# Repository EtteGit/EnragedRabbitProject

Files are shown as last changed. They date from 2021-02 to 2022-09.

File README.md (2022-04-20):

# EnragedRabbitProject

Welcome to the Enraged Rabbit Project Github page!

This project aims to bring multimaterial capabilities to 3D printers using a single Direct Drive toolhead. While this project is mainly dedicated to be used on VORON printers, it can also be used (or adapted) on any 3D printer that runs Klipper, and potentially RRF.

You like this project? You want to support me and my work, help me bring new cool stuff to the community? Well you can tip me here :


## Table of Content
- [Changelog](#changelog)
- [Showroom](#showroom)
- [Videos](#videos)
- [Details](#details)
- [BOM](#bom)
- [Acknowledgements](#acknowledgements)
- [FAQ](https://github.com/EtteGit/EnragedRabbitProject/tree/main/Documentation/FAQ)
  - [Carrot Patch](https://github.com/EtteGit/EnragedRabbitProject/blob/main/Documentation/FAQ/FAQ_ERCP.md)
  - [Carrot Feeder](https://github.com/EtteGit/EnragedRabbitProject/blob/main/Documentation/FAQ/FAQ_ERCF.md)
 
## Changelog
- **April 4th 2022 :** Minor fixes and updates, check the new last page of the manual for tuning the last check of the load sequence
- **March 23th 2022 :** Revamp of ERCF unload sequence during a print, possibility to use stallguard capabilities to detect selector blockages, new encoder cart and much more
- **October 23th 2021 :** Update of the ERCF Macros and python module and added first part of manual Slicer setting section.
- **October 15th 2021 :** Added AfterBurner Clockwork toolhead sensor and associated manual sections.
- **October 7th 2021 :** Updated SwitchWire mount, LGX on AfterBurner toolhead sensor and associated manual sections.
- **October 1st 2021 :** Update including VORON SwitchWire mount, new Galileo Clockwork Toolhead sensor, additions to the manual and a few others things!
- **September 24th 2021 :** The ERCF V1.1 macros and python module are out! Also an updated manual (with the setup and calibration steps) and additionnal stuff for EASY BRD users! Have fun!
- **September 17th 2021 :** The ERCF V1.1 assembly manual, STL files and the STEP file are now released! You'll find the manual in the "Documentation" section now, and the manual will keep growing with setup, tuning and slicer guides. A non-exhaustive patch note can be found in the Carrot_Feeder folder. Finally, note that the new software part of the ERCF V1.1 is not out yet, and the ERCF V1.1 hardware cannot be used with the ERCF V1.0 macros. V1.1 software will be released in a few days. Happy printing and assembly!
- **September 14th 2021 :** Updated the BOM to ERCF V1.1 (release coming soon! tm) and added the new, incoming Toolhead Sensor BOM (bottom tabs)
- **June 4th 2021 :** TopHatLockers and related (servo arm, TopGearHat, macros) have been released to the main branch, from the EarlyDevAccess branch. If you're already running EarlyDevAccess stuff, that won't change anything for you
- **June 2nd 2021 :** Release of Carrot Patch V1.1
   - Increased handles section near the threaded insert for more robustness
   - Removed useless chamfer on feet bottom screw holes and increased hole depth (one can now properly use M3X8 SHCS to secure the Carrot Patch on 2020 extrusions)
   - Fixed several parts lengths//size that impacted the buffer wheel installation. Now the wheel should slightly touch both side walls (to avoid any possible gaps) while being able to turn (but not freely, which is on purpose)
   - Buffer Cross bottom arm is now secured using a M3X20 SHCS screw that comes from the bottom (that is also securing the left feet of the Carrot Patch)
   - Buffer Cross ECAS insert has been tuned, reinforced and a "bridge" shape has been added. Inserting the ECAS will no longer crack the plastic
   - Increased the size of the Buffer Cross "pillar" that sits between the two PTFE paths (some users previously reported fragilities due to the lack of matter for this pillar)
   - Updated the assembly manual, BOM and the CAD accordingly
   - Only parts that did not change are : [a]_Buffer_Wheel, [a]_Latch, [a]_Sliding_Arm, Buffer_Axis, Ptfe_Entry_ECAS and Ptfe_Entry_M10

## Showroom

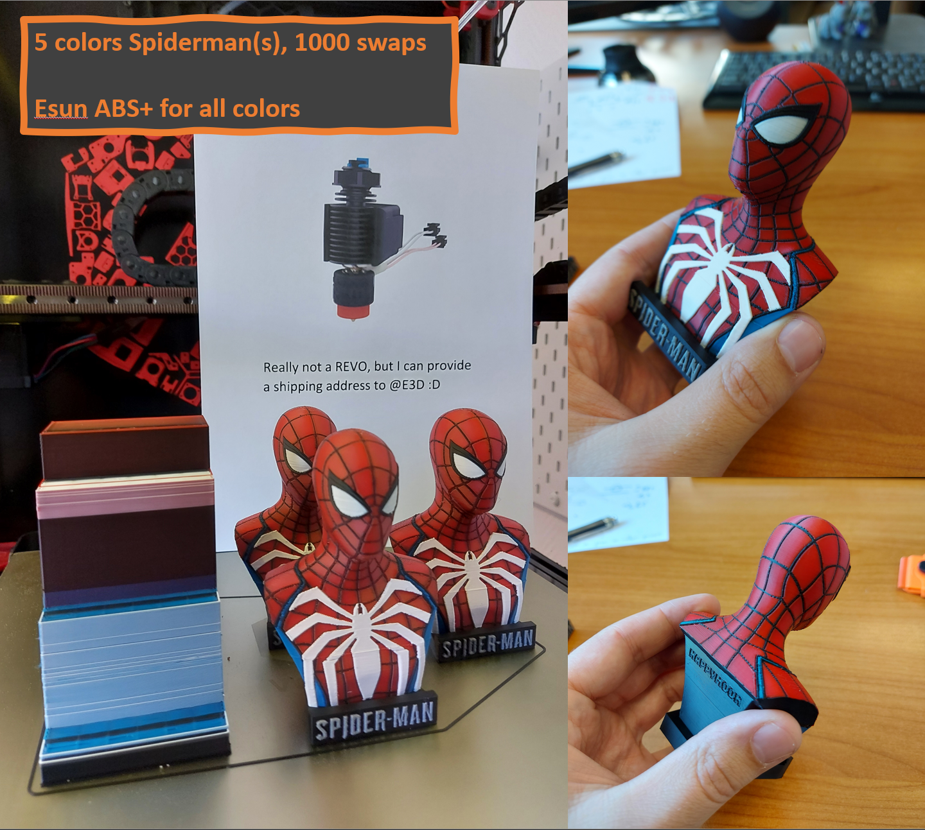
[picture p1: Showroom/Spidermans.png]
Spidermans
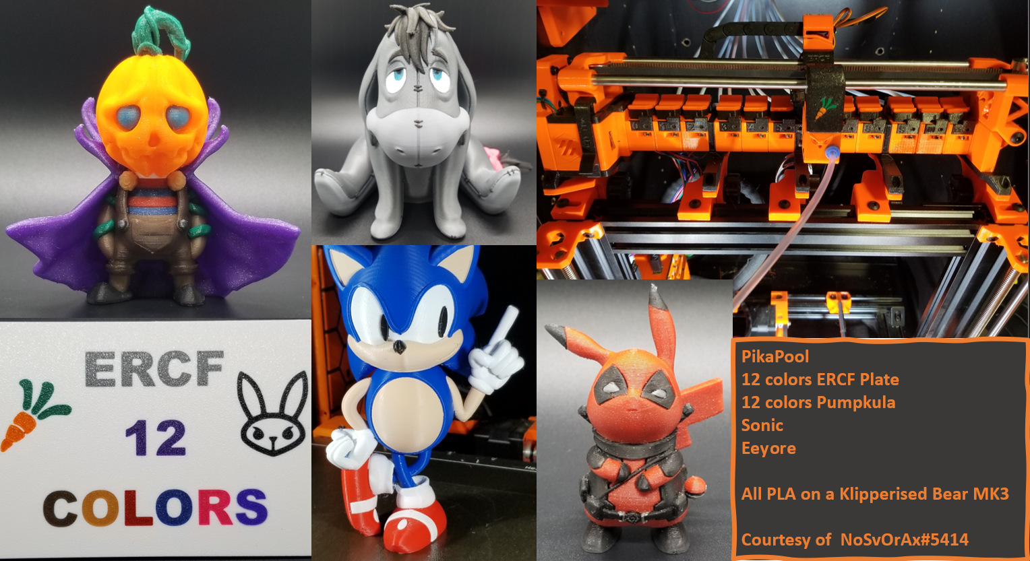
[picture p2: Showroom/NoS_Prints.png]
NoS_prints
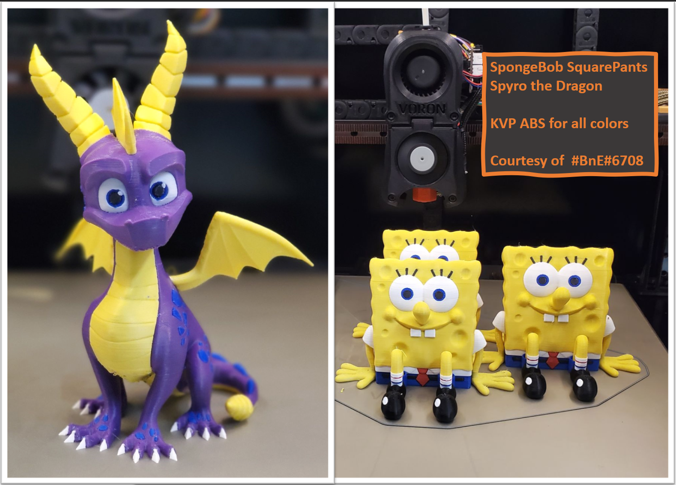
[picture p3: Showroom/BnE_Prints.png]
BnE_Prints
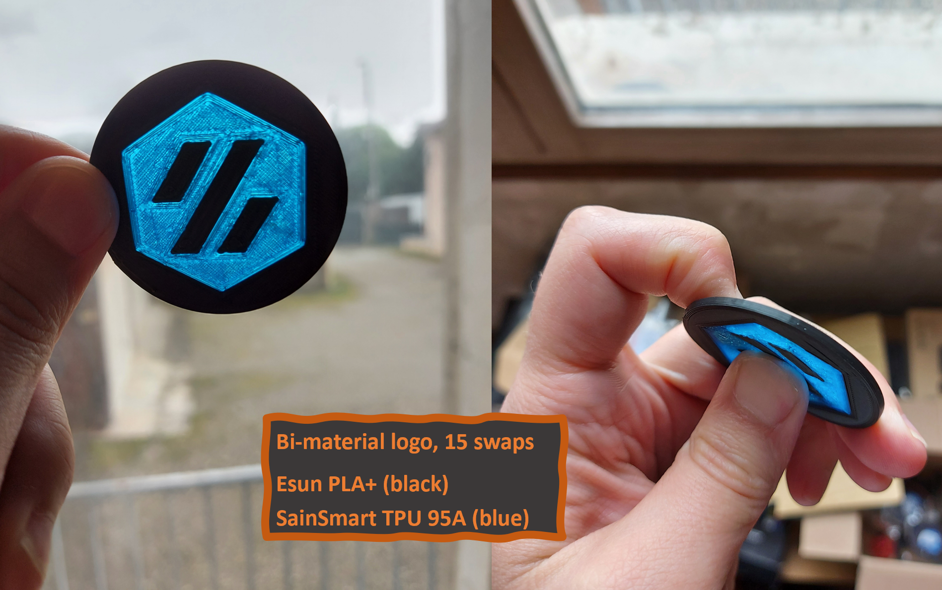
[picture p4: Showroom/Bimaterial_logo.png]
Voron Logo TPU
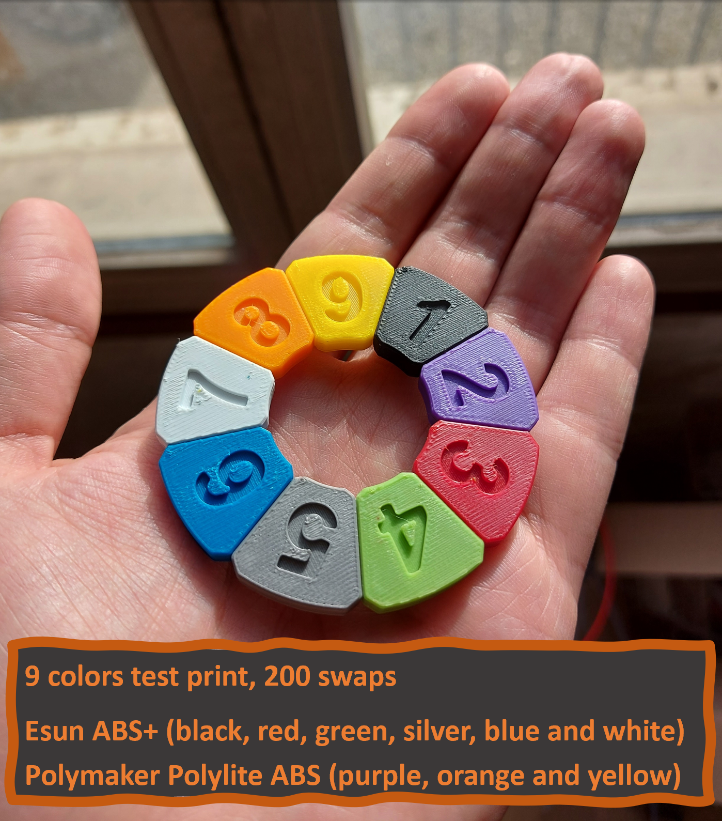
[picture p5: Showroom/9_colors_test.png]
9_colors_test


## Videos
Here are videos of the system in action. I need to release more videos...

https://streamable.com/3lo192

https://streamable.com/cjl2iz

## Details

There are 4 components so far : 
 - **The Enraged Rabbit Carrot Feeder (ERCF)**. The Carrot Feeder allows to use a high number of different filaments (tested up to 9 channels so far) and feed them, one at a time, into the printer toolhead. The ERCF gear motion system (i.e. what is used to push and pull the filament) is based on the Voron Design M4 extruder. The ERCF was inspired by the Prusa MMU2 and the Smuff.

  Carrot FeederCarrot Feeder 2
 
 - **The Enraged Rabbit Carrot Patch (ERCP)**. It is a light spool-holder and buffer combo to help you deal with the filament  
management issue associated with multimaterial systems.
 
 Carrot PatchCarrot Patch 2
 - **The Enraged Rabbit King's Seat (ERKS)**. The King’s Seat is a pellet-purge system to remove the need for a wipe-tower and make faster filament purges. This system is designed for Voron V2s only so far.
 - **The filament sensor** : a filament sensor system located below the extruder gears to check proper loading and unloading of filament.
  
Note that this is a work in progress !!
 
Only the King's Seat is yet to be released !
 
## BOM
 The BOM for those components can be found [here](https://docs.google.com/spreadsheets/d/1A_qeNeaVprh_iPbvLcLjvJ2o2NfCzjuJam3K3RkWW0w).
 
## Acknowledgements

Thanks to the VORON Design devs and VORON discord members for the discussions and support, with a special thanks to the #honhonhonbaguette-FR members and @Tircown#8715!!

Thanks to Fabreeko, DeepFriedHero (DFH), Blurolls and many others for supporting this project!

Ette

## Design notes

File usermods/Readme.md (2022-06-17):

# Mods 
This Folder contains modifications for the Enraged Rabbit

## Table structure

Update the following table with the information about your mod:
- Your name
- A link to your sub-folder
- A short description of your mod
- The component the mod is designed for. Use `:heavy_check_mark:` for :heavy_check_mark:,`:x:` for :x:

like so:
`
| Creator | [Mod title](link) | Description | :x: | :x: |`

| Creator | Mod title | Description | Feeder | Patch |
| --- | --- | --- | --- | --- |
| TheWarolf | [AB Toolhead Sensor](./AB_Toolhead_Sensor) | Makes the standard AB clockwork "smart" by inserting filament sensors in the toolhead. Uses microswitch + 7mm steel ball combo. | :heavy_check_mark: | :x: |
| Tircown | [Bearing_Block_Passthrough](./Bearing_Block_Passthrough) | Allows to do tests or add a temporary spool without taking apart the full setup while still benefit from the sensors of ERCF. | :heavy_check_mark: | :x: |
| EtteGit | [Closed_Exhaust_Plate](./Closed_Exhaust_Plate) | Replaces the nominal V2 exhaust parts with a close, sealed plate. | :x: | :x: |
| TheBelin | [EasyPatchLoader](./EasyPatchLoader) | Makes it easier to load Carrot Patch. | :x: | ✔️ |
| Drachenkaetzchen | [Extrusion Mounting Brackets](./Extrusion_Mounting_Brackets) | Extrusion mounting brackets to pre-assemble the ERCF and/or the ERCPs | :heavy_check_mark: | :heavy_check_mark: |
| Tobi0892 | [IKEA Drybox Carrot Patch](./IKEA_Drybox_Carrot_Patch) | Puts the Carrot Patch into a sealed 10.6l IKEA 365+ box to maintain ~10% humidity. | :x: | :heavy_check_mark: |
| fsironman | [JST-SM-Connectors](./JST-SM-Connectors) | Modifies the M4 Arm to use JST-SM instead of microfit connectors | :heavy_check_mark: | :x: |
| simon-adriaanse | [LGX_Mount_TL_IR_Sensor](./LGX_Mount_TL_IR_Sensor) | This mount is for the TriangleLabs IR sensor. | :heavy_check_mark: | :x: |
| th3fallen | [LGX_Toolhead_Sensor](./LGX_Toolhead_Sensor) |  | :heavy_check_mark: | :x: |
| Falovan | [Narrow KVP Spool Ramp](./Narrow_KVP_Spool_Ramp) | Adds a ramp to the carrot patch to prevent narrow spools from catching | :x: | :heavy_check_mark: |
| th3fallen | [Orbiter_Toolhead_Sensor](./Orbiter_Toolhead_Sensor) |  | :heavy_check_mark: | :x: |
| jorender | [Printable_drag_chain](./Printable_drag_chain)  | A printable cable chain suitable for use with the Enraged Rabbit Carrot Feeder | :heavy_check_mark: | :x: |
| claytono | [Skirt-Microfit-Inserts](./Skirt-Microfit-Inserts) | An iteration on dvorak74's Micro-Fit inserts, based around meteyou's fantastic G-code button mod. | :heavy_check_mark: | :x: |
| Drachenkaetzchen | [Upside Down ERCP](./Upside_Down_ERCP) | Mod to allow mounting the ERCP upside down, for example, below a shelf | :x: | :heavy_check_mark: |
| str1pes | [MagFeet](./MagFeet) | Easy mounting/removal for 2020 extrusions | :x: | :heavy_check_mark: |
| joey2point0 | [4L_Filament_Buffer](./4L_Filament_Buffer) | Utilizes 4L cereal box container to make a sealed filament buffer. | :x: | :heavy_check_mark: |
| ~MHz | [Orbiter_V1.5_V2_on_AB](./Orbiter_V1.5_V2_on_AB) | Yet Additional Orbiter v1.5 Mechanical and Inductive Extruder to Toolhead adapter and a WIP Orbiter v2 Inductive Extruder to Toolhead adapter  | :heavy_check_mark: | :x: |

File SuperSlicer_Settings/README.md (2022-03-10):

# SuperSlicer settings

I'm using SuperSlicer (https://github.com/supermerill/SuperSlicer) with my ERCF.

Here is a collaborative, open table to share [proper purging volumes](https://docs.google.com/spreadsheets/d/11onBwd85u0-9houRi6wMT2FBWrvbKk8fzwE3qLjkN1w/edit?usp=sharing). Please respect the table layout and don't delete//edit other people's inputs :) .

Here are my SuperSlicer settings related to the multimaterial :

## Printer Settings
#### Custom G-code
Tool change G-code : T[next_extruder]

#### Single extruder MM setup
Cooling tube position : 40mm
Cooling tube length : 20mm
Filament parking position : 85mm
Extra loading distance : -83mm
High extruder cyrrebt on filament swap : off

Important : those settings are tested for a Dragon Normal Flow hotend! If you have a different hotend, you'll have to tune those numbers.

## Filament Settings

Each filament (brand, type or even just color) behaves differently. The goal of tuning those filament settings is to end up, at every single filament change, with a nice filament tip.

What is a nice filament tip?? It's a tip withtout long hairs, without blobs, with a proper, well defined, diameter. It should more or less look like a nice spear end.

Filament tip tuning is THE MOST IMPORTANT setting in your MMU setup, period. So take the time to tune those, it's really worth it!
The default filament settings associated with the PrusaMMU2S profile in prusa//super slicer are a very good starting point!

Esun ABS+ : use default multimaterial settings from the MMU2S profile (PrusaABS filament profile), and add a skinnyDip string reduction sequence with 42mm insertion distance, 0ms of pause, 33mm/s speed to move into the melt zone and 70mm/s speed to extract from the melt zone

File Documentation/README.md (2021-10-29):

# Enraged Rabbit Project Documentation

All the manuals for assembly, setup and tuning related to the Enraged Rabbit Project are here.
You can also find the FAQ in its dedicated folder.

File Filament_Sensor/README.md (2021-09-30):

Readme for Filament Sensor

# General guidelines and informations
The toolhead sensors are based on a hall sensor, design is from @Tircown.

Galileo ClockWork is available.

AfterBurner ClockWork and LGX on AfterBurner will be released soon.

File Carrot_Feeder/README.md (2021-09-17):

# ERCF V1.1 Patch Note (non exhaustive)
This is a major update. If you already have a, ERCF V1.0, please reprint all the parts for V1.1. Feet anchoring points are unchanged.

## Hardware:
### Filament Blocks:
- Updated filament path to limit unselected filament being pulled or pushed by the rotating gear. The grip on the filament is also drastically improved
- Fixed the ECAS insert slot
- Removed the threaded insert version as the direct plastic tapping was sufficient
- New and improved number tag plate (easy to install and remove, much more robust than before)
- Added magnetic gates at the exit of each filament block : using a M3 Steel washer and magnets, the filament path of each filament block will be closed at the filament block exit when the selector is not in front of it, ensuring that no unselected filament can stick out and block the selector cart during a tool change
### Top Hats :
- Redesign of the Top Hat arm to avoid it's ejection when opening the filament block latch
- Top Hat Lockers are now easier to print (more contact area with the print surface)
- New slide-in mechanism for the Top Hat Lockers
- Top Hat Locker will no longer touch the Filament Block Latch, which is no only touching the Top Hat
- BMG gear can no longer be installed in the wrong orientation in the Top Hat
- Moved the servo pressure point on the Top Arm Locker to have a better grip on filament
### Gear Box :
- Gear motor is now a low rotor inertia NEMA 14, allowing a smaller footprint, quieter operation and faster loads and unloads (NEMA 17 motors are still 100% compatible)
- Added a bearing on the Gear Box Back to better constrain the 5mm D-Cut shaft and remove potential longitudinal play
- Motor Arm infamous overhang is now easy to print
- Added a customisable, multicolor logo on the front, which is easy to change
- Minor fixes (micro switch lever colliding with 3D printed part, more plastic matter behind the left side latch threaded inserts...)
### Bearing Blocks :
- Added foot to improve global stiffness, especially for long units. It can be install and removed easily without dismounting the unit
### Selector Motor Support :
- Fixed the 8mm rod hole issue (same for the Idler Block)
- Fixed the selector motor screws issue
### Selector Cart :
- Old filament sensor is gone. Now there is an amazing encoder, idea and design by @Tircown! Encoder fits in the ERCF selector cart, has a 1.3mm resolution and can keep up with very fast movement (20cm/s +). Allows to precisely track filament load and unload, potential clogs during a print and is also used as filament runout sensor
- New servo ref. Easier to source, quieter and much cheaper than V1.0 model, works well with the new Top Hat Locker and - Filament Blocks design. V1.0 servo model is still 100% compatible
- Mystery stuff hidden behind the new selector cart door, can you guess what it is from the charade hidden in the ERCF?

## Software:
To use the new selector encoder, part of the software have to be done in the python part of Klipper. The ERCF V1.1 software will now include a .py file and the usual cfg files. The GCODE macros are still in use, but are much smaller.

Regular update and improvements will be done on the software side, as using the python part of Klipper allows for much more complex and fancy stuff to be done.

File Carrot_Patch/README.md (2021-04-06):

This directory contains the files necessary to print and construct the Carrot Patch spool holders.

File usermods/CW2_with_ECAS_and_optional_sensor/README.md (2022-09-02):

## Clockwork 2 with ECAS fitting, with or without ball bearing filament sensor

This version of the Clockwork 2 extruder adds an ECAS fitting to the filament
input port. The ECAS serves the same purpose as a screw-in PC4 fitting: to retain
the PTFE tube during ERCF operations so it doesn't pop out. 

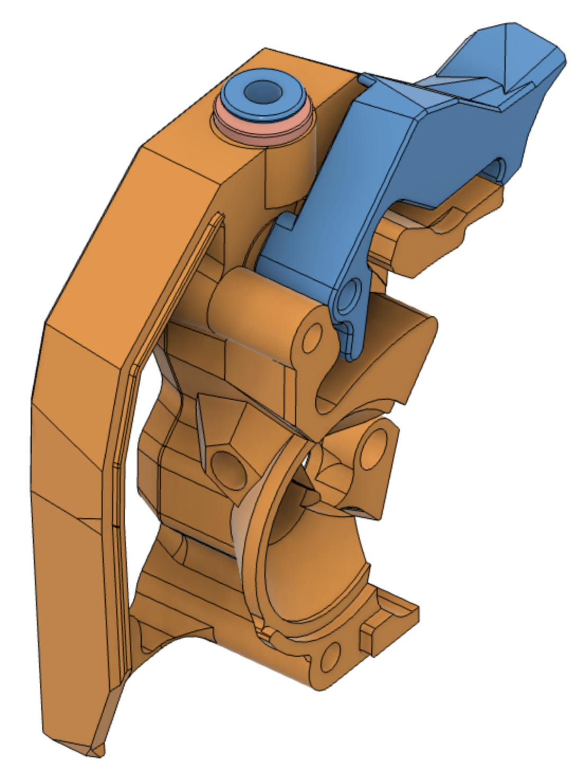
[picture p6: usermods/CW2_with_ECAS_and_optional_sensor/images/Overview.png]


Optionally, you can print a version that includes provisions for a mechanical filament
sensor that uses a ball bearing and microswitch. See below.

The basis for these designs is the VoronDesign/Voron-Stealthburner project on GitHub as
of August 18, 2022, git commit b2cf2c2. Here are a
[link to that commit](https://github.com/VoronDesign/Voron-Stealthburner/tree/b2cf2c2c0436d734181688ae3019b9dffb835b8b) 
and a [link to the current version](https://github.com/VoronDesign/Voron-Stealthburner) 
of the Voron-Stealthburner project.

The version of Voron-Stealthburner on which this mod is based postdates RC1. 
Both the CW2 main body and the 
latch have been updated relative to the RC1 release of Voron-Stealthburner.
However, RC1 versions of other parts **are** compatible with this main body and latch.

The parts in this mod **are not** compatible with pre-RC1 versions of the Clockwork 2.
Please see the pinned mod in the Discord #ercf_questions channel if that's the CW2
you want to modify.

## ECAS-only (no filament sensor)

For the ECAS-only version, you just need to print the main body
and the latch. The rest of the parts are identical to the standard CW2.

Press-fit the ECAS into its dedicated hole as described in the ERCF documentation. Done!

## ECAS and filament sensor

The filament sensor included here uses a 7mm ball bearing and a standard microswitch. It
is *not* a direct port of the standard ERCF toolhead switch, which uses a Hall-effect sensor.
The mechanical version seems to be somewhat less susceptible to jamming and misreading.
However, it does introduce a small amount of friction on the filament path. 

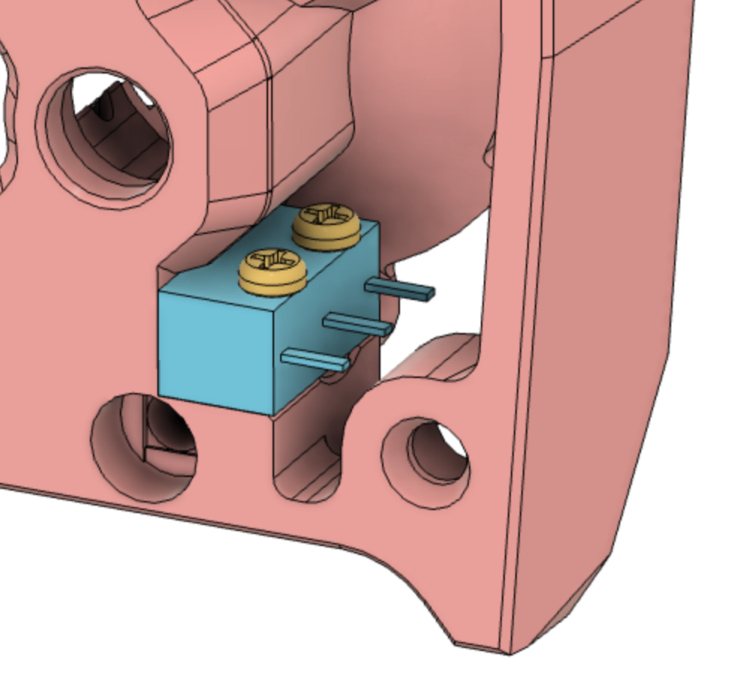
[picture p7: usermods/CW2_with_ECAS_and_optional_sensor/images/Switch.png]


### Bill of materials

You will need:

- An Omron D2F-series microswitch with lever, or equivalent (e.g., D2F-01L, see below)
- Two M2x10 self-tapping screws
- One 7mm ball bearing (stainless steel is fine, does not need to be magnetic)
- One ECAS fitting

According to Omron's CAD files, the plunger on
a D2F without a lever is shaped slightly differently from the plunger on a lever
switch. This mod is designed for a lever switch even though the lever isn't used. 
Plunger-only
switches might work fine. I just don't know for sure.

The mod also assumes that the switch's operating force is the standard 1.47 Newtons.

See Omron's [D2F data sheet](https://components.omron.com/us-en/datasheet_pdf/B036-E1.pdf)
for details on decoding all the variants of this switch. The model number should end with an
L and should not contain an F. Any voltage or current rating is fine. You probably want
standard PCB terminals, but any variant should work. However, be sure not to block the
cutout next to the switch, as that's a through-way used when bolting the CW2 to the
carriage.

### Operating principle

Here's a cutaway view of the sensor when assembled:

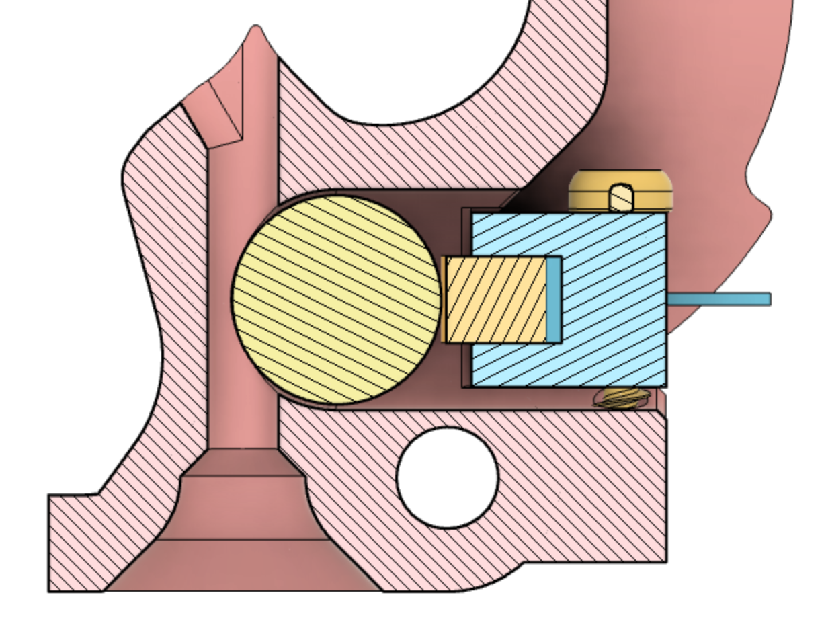
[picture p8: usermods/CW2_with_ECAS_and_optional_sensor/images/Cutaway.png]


The ball bearing intrudes into the filament channel. When filament is present, it
pushes the bearing aside, causing it to activate the switch. 

### Assembly instructions

- Remove the lever from the switch. 

- Print the test block.

- Insert the ball bearing into the test block. It should pop in with just slight pressure.

- Screw the microswitch into the test block. Make sure the plunger of the microswitch is 
centered on the bearing. For Omron switches, the side with printing on it should be down.

- Make sure that filament can easily be inserted (even with a blunt end) and that 
the sensor assembly does not
add excessive friction.

- Use a multimeter to verify that the switch consistently activates when filament is 
present and deactivates when filament is removed.

- If you have problems with friction or failure to register filament, see the section
below regarding alternate STLs.

- Print the main body and the latch.

- Press-fit the ECAS into the top of the main body.

- Solder two wires to the switch and cover them with heat-shrink tubing.
Use the two outer leads for normally-closed mode, which is recommended.
Ignore or cut off the middle lead.

- Install the ball bearing and switch in the main body of the CW2.

- Install the new main body and latch on your CW2.

- This mod shortens the bottom end of the filament path by 3mm. So 
shorten the stub of PTFE tubing coming out the top of your hotend cartridge by 3mm.

- Once the new parts are installed on the CW2, you can bend the PCB leads coming 
out of the switch to direct the wires more naturally. Not much bend is needed if
you are using a standard cover and PCB.
Do not bend the switch leads downwards so
that they interfere with the wrench path for attaching the CW2 to the carriage.

- Add the appropriate connector to the other end of the wires, hook up, and configure
in the ERCF control files for Klipper.

### Alternates

If the test block seems to indicate that filament won't be reliably detected, or 
will be unreasonably pinched by the ball bearing, you can try the "tight" or "loose" 
variants from the Alternates folder.

- The tight version moves the ball bearing channel and the switch further
*into* the filament path. This *increases* friction, makes it *harder* to get 
filament past the ball bearing, and makes it *easier* for filament
to activate the switch.

- The loose version moves the ball bearing channel and the switch further
*out of* the filament path. This *reduces* friction, makes it *easier* to insert filament, 
and makes it *harder* for filament to reliably activate the switch.

I don't yet have data on other people's experience with this filament sensor design.
My hope is that the standard configuration will cover nearly all cases, but 
filaments and tuning
vary. The loose and tight versions are just there to give you a backup plan. Stick 
with the standard version unless you're encountering specific issues.

## Bug reports and suggestions

For problems or suggestions, you can file a GitHub issue against 
[my fork of the ERCF project](https://github.com/GarthSnyder/EnragedRabbitProject).

I am @Iatrodectus on Discord and @GarthSnyder on GitHub.

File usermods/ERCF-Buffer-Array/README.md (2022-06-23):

# ERCF-Buffer-Array

The Carrot Patch for the Enraged Rabbit Carrot Feeder has an integrated spool holder included. For people who store their spools in a drybox, this can be an issue. Either you have to store the buffer ring also in the dry box, which takes away space for filament spools, or one has to design a dedicated solution for the buffer ring outside of the dry box.

The Buffer Array solves this issue by dropping the spool holder and allows stacking up buffer rings side by side, called Buffer Array. One buffer ring element takes up 40mm of space (normal version) or 33.5mm (slim version). The Buffer Array is based on a modified main body so that all other required parts of the carrot patch can be re-used. The Buffer Array is modular an thus can be adapted to the size of your ERCF. For up to N=6, I also provide an integrated solution vor the V2.4, see image below.

Building a Buffer Array of length N>1 requires:
- the standard Carrot Patch parts:
  - 1x 608_Adapter.stl
  - 1x Buffer_Axis.stl
  - 1x Buffer_Cross.stl
  - 1x Buffer_Wheel.stl
  - 1x feet_x2.stl or Feet_cut_off.stl
- 1x "Buffer Array Start"
- (N-2)x Buffer Array Middle
- 1x Buffer Array End
- recommended for stability: multi-locker with or without guide for ptfe tubing
- 1x M5x30mm and 1x m5 lock nut
- 1x M3x20mm, 1x M3x8mm, 2x M3 heat insert (Voron version M3x5x4)
- 608ZZ bearing

If you already have old carrot patches, then you can recycle all parts except the heat inserts!
If you want only N=1 then there is also "Buffer array Stand-Alone" available.

If you want to integrate an 6x ERCF with buffer array and spool holder on your back of your V2.4 (350mm), then use the special multi-locker and spool holder in the " V2.4-Integration", see image below.

RL Triple Buffer Array

RL Triple Buffer Array

Overview Main_Body Types

Overview Main_Body Types

Overview Main_Body Types

V2.4-Integration

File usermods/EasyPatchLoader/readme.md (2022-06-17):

# ERCP Easy Load Buffer Wheel

This buffer wheel replaces the existing buffer wheel.

## To Load:
1) Feed the filament through the load tube.
2) Push the filament end into the slot on the side of the wheel, the curved profile should keep your filament secure.
3) Turn the wheel to load the buffer your required amount.
4) Position the wheel near the buffer exit fitting.
5) Unclip the end of the filament from the wheel and push it into the ERCF feed tube.

[Download STL](./STL/[a]_Buffer_Wheel_EZ_Loader.stl)

## Images
Easy Load Buffer Wheel
Easy Load Buffer Wheel Step 1
Easy Load Buffer Wheel Step 2
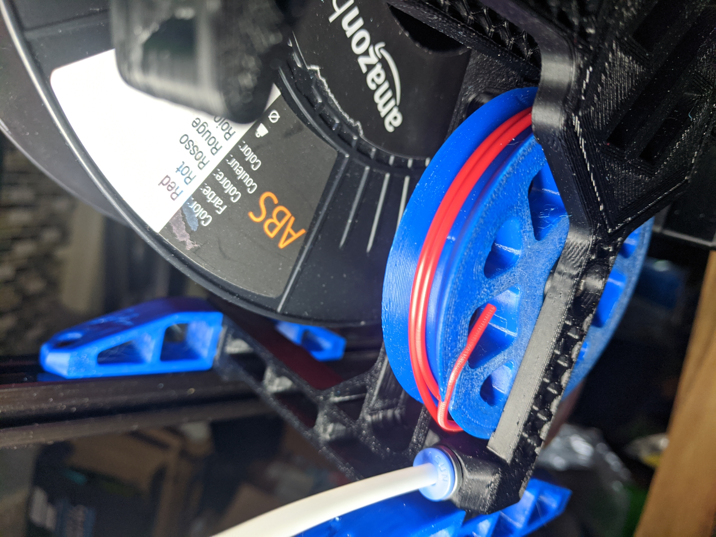
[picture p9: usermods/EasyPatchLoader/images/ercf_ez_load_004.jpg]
Easy Load Buffer Wheel Step 3

Easy Load Buffer Wheel Step 4
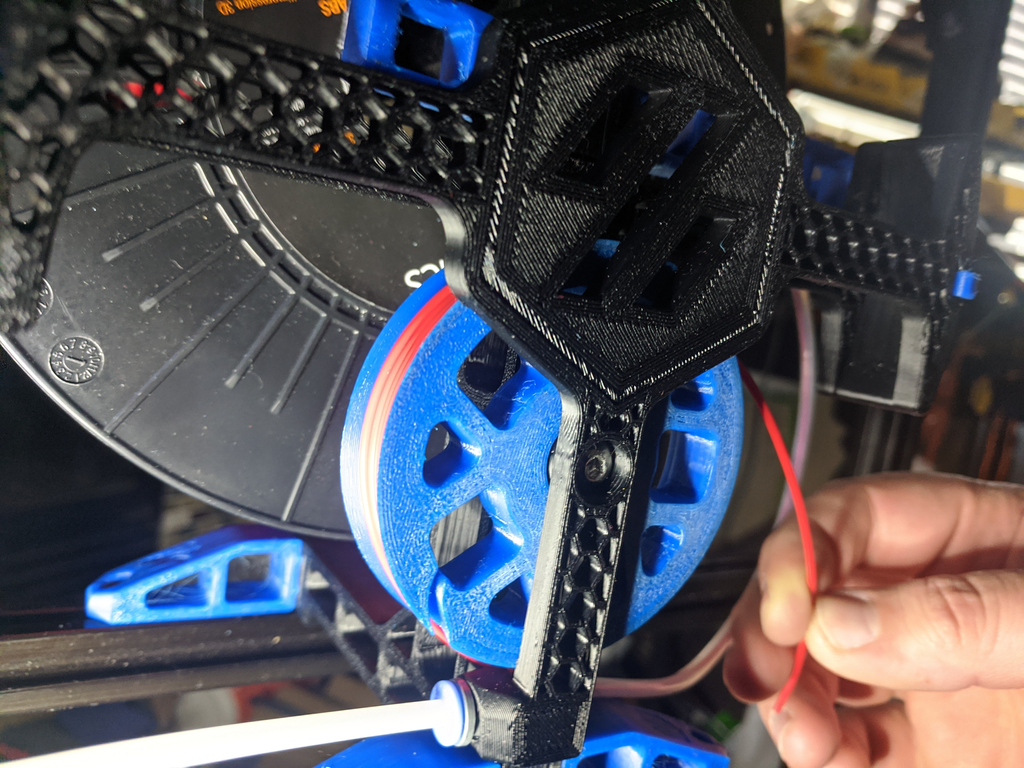
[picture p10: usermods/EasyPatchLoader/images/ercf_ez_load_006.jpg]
Easy Load Buffer Wheel Step 5


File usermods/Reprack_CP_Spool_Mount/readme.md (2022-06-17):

Carrot Patch spool mounting bracket for the [RepRack filament holder](https://www.prusaprinters.org/prints/129024-reprack-open-source-spool-holder-and-storage-syste). This is a cheap way to mount a bunch of filament to the wall above your printer.

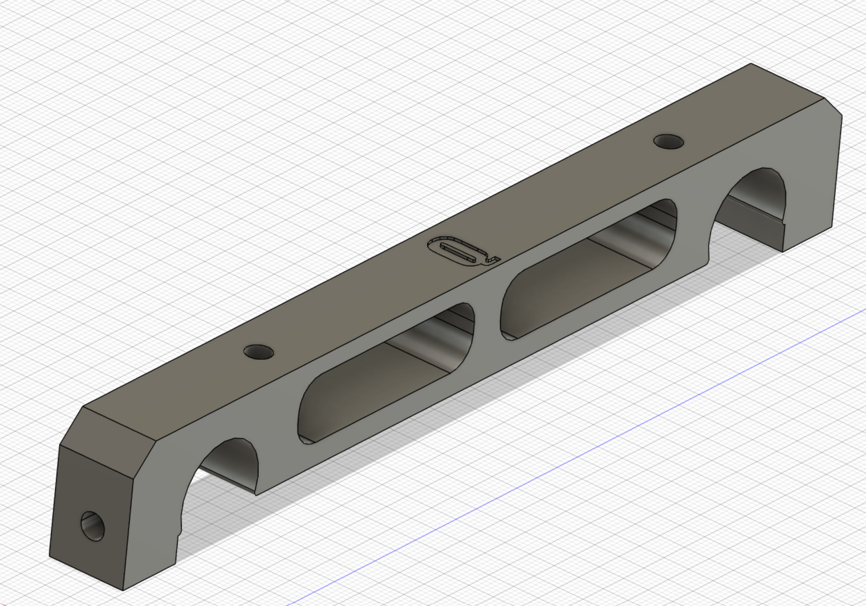
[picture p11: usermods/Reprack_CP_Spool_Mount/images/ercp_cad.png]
Fusion 360 Screenshot of the mount


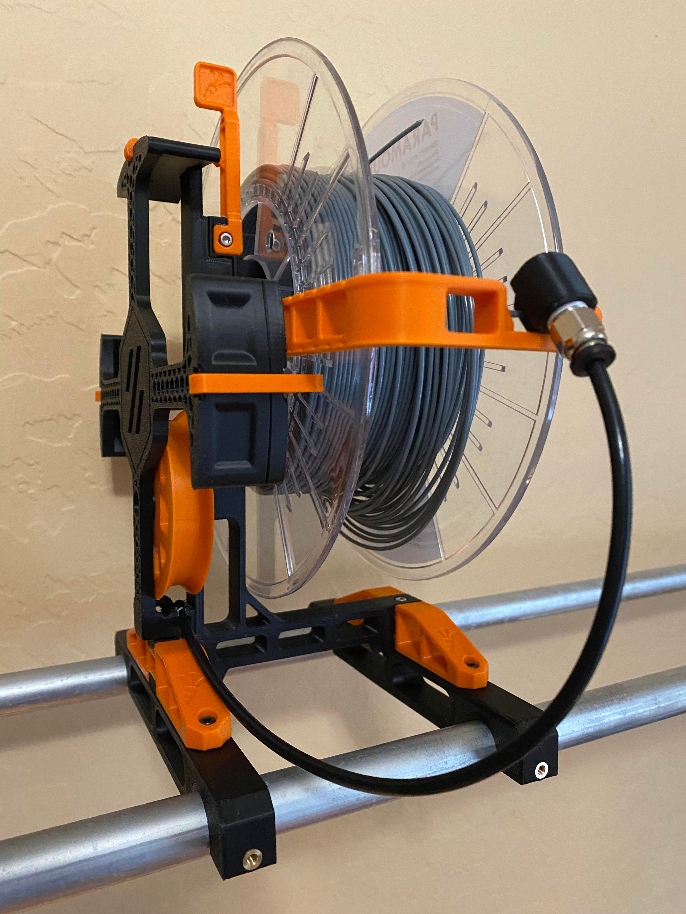
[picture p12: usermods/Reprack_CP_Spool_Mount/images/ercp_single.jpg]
Picture of a single fully assembled ERCP mount


# Assembly Instructions

1. Print as many mounts as you need
2. Install M3 heat inserts into the top two holes, and the side hole. Pro-tip: attach the heat insert using a short M3 bolt as a guide.
3. Attach the Carrot Patch spool with two M3x8 screws
4. Place the spool holder on the RepRack, optionally secure it with the front mount

# Version
* Version for non-covered tube: [Regular Version](RepRackErcfMount.stl)
* Version for Slip Rod Covered tube: [Slip Rod Compatible Version](RepRackErctMount_SlipRod.stl)

# Credit
* Regular Version: Designed in Fusion 360 by Danny Quist Discord: chamcham#6574
* [Slip Rod](https://www.printables.com/fr/model/135700-slip-rod-cover-for-reprack-and-repbox) compatible version: modified in ThinkerCAD by Flisher on Discord

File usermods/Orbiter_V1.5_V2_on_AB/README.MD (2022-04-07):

Here are some cobbled up ERCF tool head sensors:

- inductive filament sensor/adapter for mounting the Orbiter v1.5 (and v2?) on the AB.
- mechanical filament sensor/adapter for mounting the Orbiter v1.5 on the AB.

The Orbiter V2 inductive sensor adapter is a remake of the same thing on the Orbiter 1.5 I originally did for myself.

I've tested and was using the inductive Orbiter 1.5 on V2.2526.  However, due to suspected thermal sensitivity (while it worked 100% outside of the printer), once installed and heated, reliability dropped substantively.  As such, I have since migrated to a bearing/microswitch setup and have had zero reliability issues since then.  Mechanical is the way to go here, I perceive.

The inductive Orbiter 2 is an alpha/beta/POC until it is tested and proven to work.  One user mentioned slight variances of the two main mount holes, but never got back with required geometry changes.

Print in the orientation depicted in the project files - no supports needed.  I used ABS with a typical Voron profile (240/120 temps, 0.4 noz, 0.2 LH, 4 walls, 5 top/bot layers, 40% infill, ...).

## For the inductive flavor:

Inductive BOM needs:  1ea/2ea 6x3 magnets, one of the iron washers used in the gates, the hall effect sensor in the ERCF kit, 6ea M3 heat inserts, a M3x8, the printed extruder adapter parts (2 pcs total), and 2 short bits of bowden tube:

- one 8.25mm piece from the Extruder into the throat of the adapter 
    - https://i.imgur.com/SoOvUEF.jpeg
- one 20.25mm(?) piece between the adapter into the throat of the hot end
    - https://i.imgur.com/e6WDewI.jpeg

NOTE:  Before I switched to the mechanical switch, I planned to double check these measurements when next I had the extruder removed from the tool head, but that never happened.  These tube measurements are relevant in the context of an Orbiter v1.5 on the attached adapter and a traditional AB install of a Dragon HF HE.  If you are using a different HE, then start out with a longer lower tube length and trim down in an iterative manner to arrive at a snug fit.  If one is using the Orbiter v2, then follow a similar process to arrive at the correct length of the upper tube.  In any case, if you are able to advise, I'll add those lengths herein for different HEs or for the Orbiter v2, to help peeps wishing to make use of same.

ERCF assy manual page 80/81 are applicable as it relates to the innards.

I added a JST 2.0 3-pin connector after I hobbed out some material to make room for it (post processing ya know...), but one could just run wires to an inline disconnect at the tool head or similar.

https://cdn.discordapp.com/attachments/928716501480009768/938473912537350194/2022-02-02-11-36-55.png

ERCF Manual shows only 1 magnet.  I ended up needing to stack 2 (the top one is a bit proud but space isn't an issue on the 1.5 mounted to an AB carriage with this adapter).  https://i.imgur.com/W8hy9hX.png

There's some dialog about the sensor being pole sensitive, so maybe that is why I had to use two.?.  w/e - it works...  

https://cdn.discordapp.com/attachments/928716501480009768/938505236845330472/20220202_134303.mp4

EDIT:  Besides the sensitivity of the hall effect sensor wrt N/S poles of the magnets,  there are different magnet types and numerous types of hall effect sensors.  The hall effect sensor model that is in the kit has been vetted by Ette for stability and use as the tool head filament detector in the hot environment of an enclosed Voron print volume (it's rated to 150 C).  Also, note that these hall effect sensors are open drain devices - presenting a hi-z open when there is no filament detected and connected to ground when filament is detected.  This means that the signal input to the MCU should have the internal pull-up enabled (^) and have inverted logic enabled on said input (!):  https://i.imgur.com/XfR8kqq.png 

## For the mechanical flavor:

A .stl is provided.  If one desires to see how I did this in PS from a blank adapter, I have also provided a .3mf project file.  The .3mf needs to be opened and sliced in Prusa Slicer >=v2.4.1, as it makes use of Negative Space Modifiers to redact material from a blank adapter model for the bearing cavity, the microswitch/attaching screws, the JST 2.0mm 3-pin male header, and the wire path from the switch to the JST (I used 30awg silicone insulated (wirewrap) wires for same.  I slice the model and saved the gcode.  I then used Voxelizer to take the gcode and create a .stl from the sliced gcode.  The back way around, admittedly, but it works and helps me to avoid learning 3D CAD that much longer... ;)

BOM:

- 1ea printed adapter set (both front and back models)
- an Omron D2F-01 or similar (typical endstop switches)
- 2ea self-tapping M2.5 x 10mm screws
- 1ea 4mm (or 4.5mm*) Bearing
- 1ea JST 2.0 3-pin connector pair (male on the adapter, female on wire side)
- ~6" of 30AWG silicone insulated (or similar) wire

*The bearing cavity/throat was originally designed for a 4.5mm bearing, as I thought I had them on hand but nope, so I made use of a 4mm bearing and have experienced no issues.  It just works.  It's so much better than fighting with lines of flux... ;)

## Happy Printing!

Enjoy.

~MHz

(P.S.  Don't judge.  lol.  These were cobbled together from several models using Prusa Slicer as a CAD alternative.  I have absolutely zero/naught/nil 3D CAD skills, so this is the best I am capable of ATM. 🙂 )

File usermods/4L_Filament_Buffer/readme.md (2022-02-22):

# Filament Buffer Drybox - BETA

This buffer solution is still heavliy in beta, changes to the design will come out as issues and areas of improvement are identified.

[Link to repo](https://github.com/joey2point0/Filament_Buffer_Drybox)

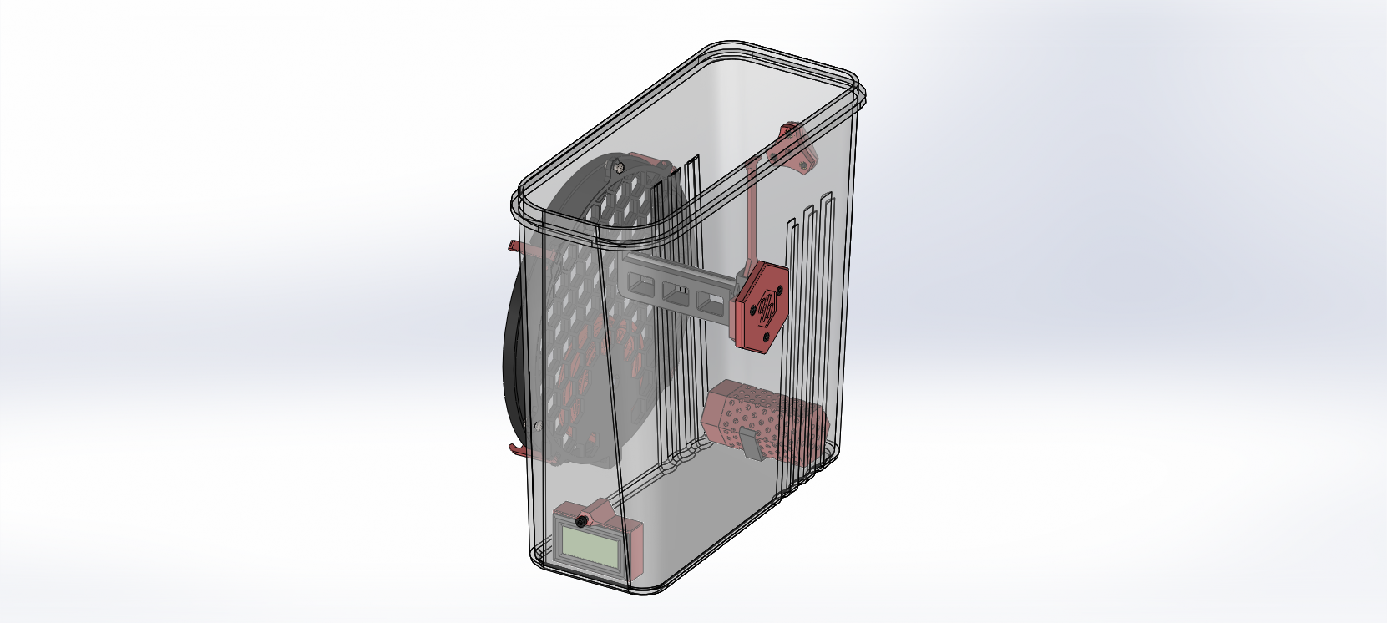
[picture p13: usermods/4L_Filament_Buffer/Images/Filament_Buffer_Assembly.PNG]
Filament Buffer Assembly


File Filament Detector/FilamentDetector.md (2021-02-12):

Readme for Filament Detector

# General guidelines and informations
Right now only the Galileo clockwork version prior to the latest release of beginning of February 2021 is available.
Version for the newest Galileo clockwork will be done soon, and so is the version for the regular Afterburner.

Check the assembly manual in this folder.

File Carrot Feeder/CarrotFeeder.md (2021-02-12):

Readme for the Carrot Feeder

# Printing guidelines
Use typical Voron parts printing guidelines (as found on the Voron Discord). No supports are needed.

For the Filament_Block part, you have the choice to use either the insert version or the no insert version. The M3 threaded insert on this part is tricky to insert, so you can simply screw the M3x16 in the plastic if you prefer. There are no real efforts on this screw, so choose the version you prefer (I prefer the threaded insert).

The support feet are either in 4mm or 5.5mm, depending on the Top//Back plate of your Voron.

The 'dome overhang' on the M4_Gear_Arm is an extreme torture test for the overhangs. It will probably not look good (but if your printer is properly tuned it will be ok). It's ok though, just clean it slightly if need be, you just don't want "stuff" hanging around.

You can use any number of Bearing_Block in your system, and wherever you want in-between your Filament_Blocks. Though the bar lengths from the BOM are calculated assuming you are using one Bearing_Block (of 5mm width) per 3 Filament_Block, starting from 3 blocks (i.e. 0 Bearing_Block for 1 to 3 channels system, 1 Bearing_Block for 4 to 6 channels systems etc.).

# Assembly
A pdf for the assembly will be released soon, as well a videos to show you a full build//installation and calibration, just be patient!

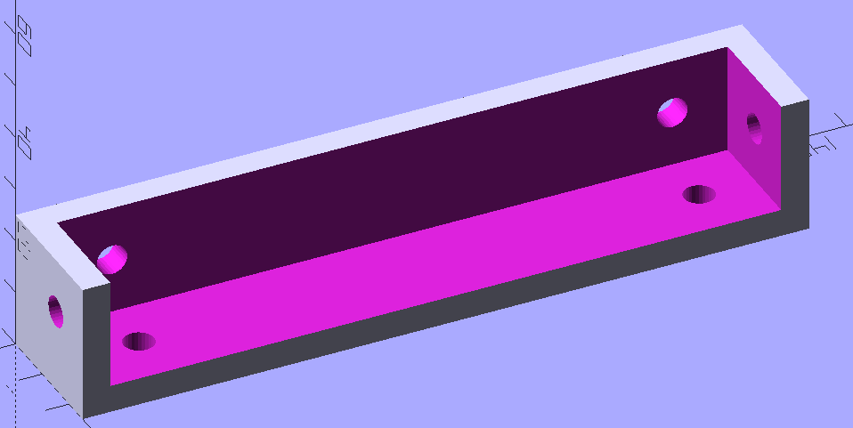
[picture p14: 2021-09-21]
usermods/Extrusion_Mounting_Brackets/images/Extrusion_Brackets.png

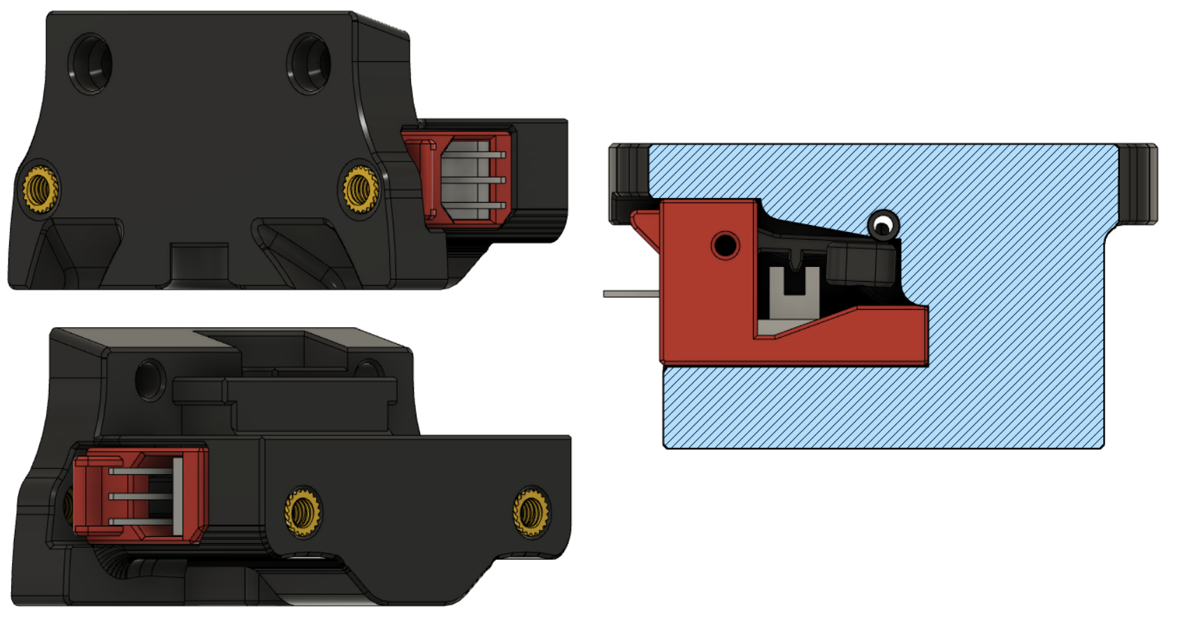
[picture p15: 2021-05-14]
usermods/LGX_Mount_TL_IR_Sensor/Images/Render.png

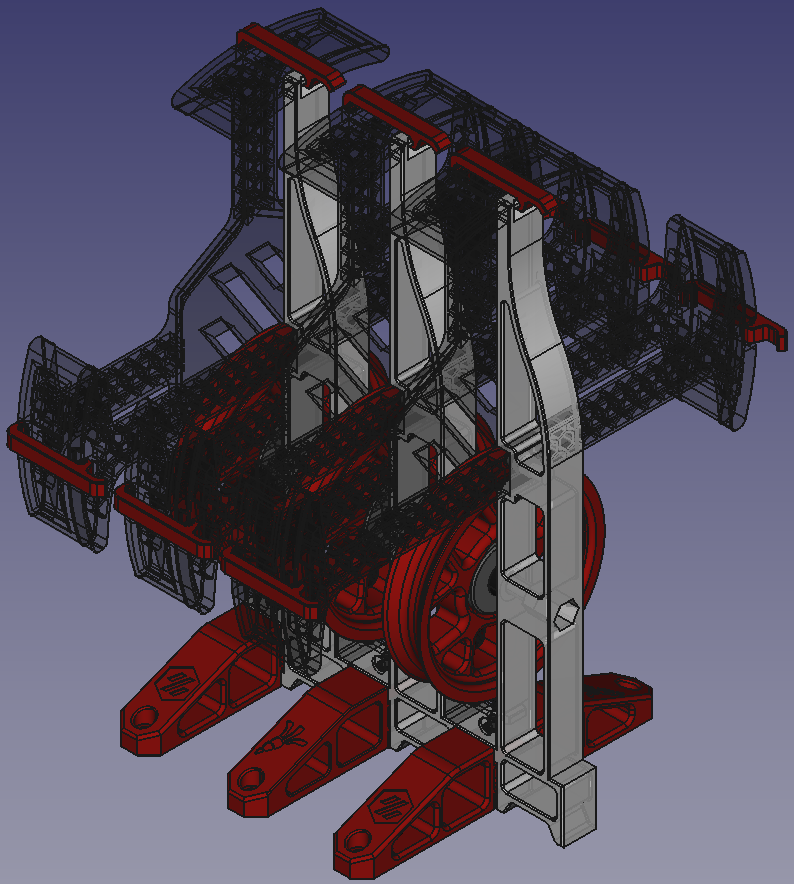
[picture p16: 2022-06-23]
usermods/ERCF-Buffer-Array/images/CAD-triple-buffer-array-iso.png

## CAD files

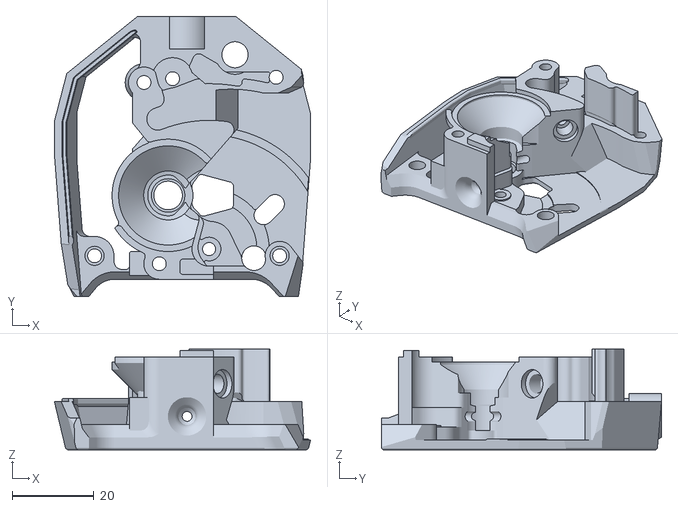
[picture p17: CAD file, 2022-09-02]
usermods/CW2_with_ECAS_and_optional_sensor/STL/Alternates/main_body_with_ECAS_and_sensor_tight.stl
62.8 x 68.7 x 24.7

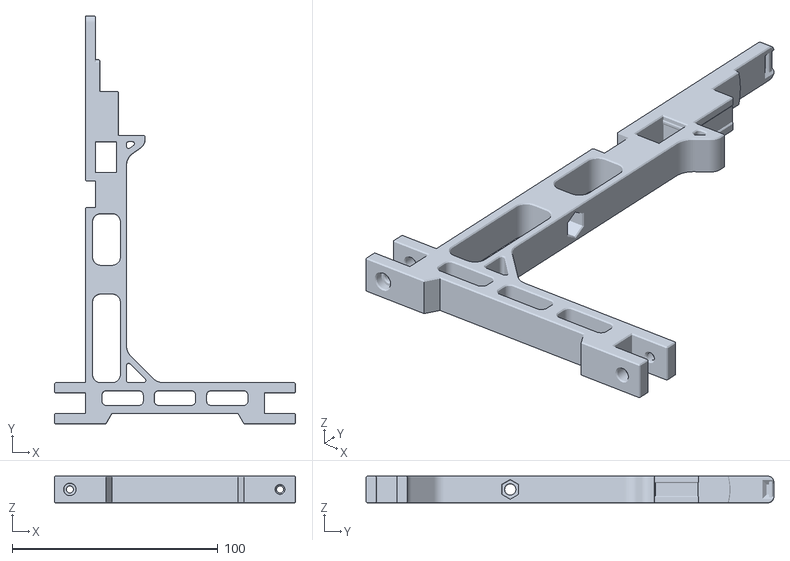
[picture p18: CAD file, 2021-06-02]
Carrot_Patch/STLs/Main_Body.stl
117.0 x 198.0 x 13.0

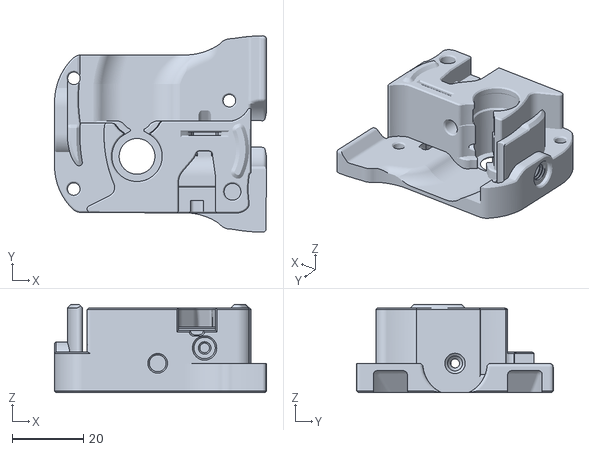
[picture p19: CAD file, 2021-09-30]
Filament_Sensor/Stls/Galileo/Galileo_ERCF_Sensor_Main_Body.stl
59.4 x 55.0 x 24.7

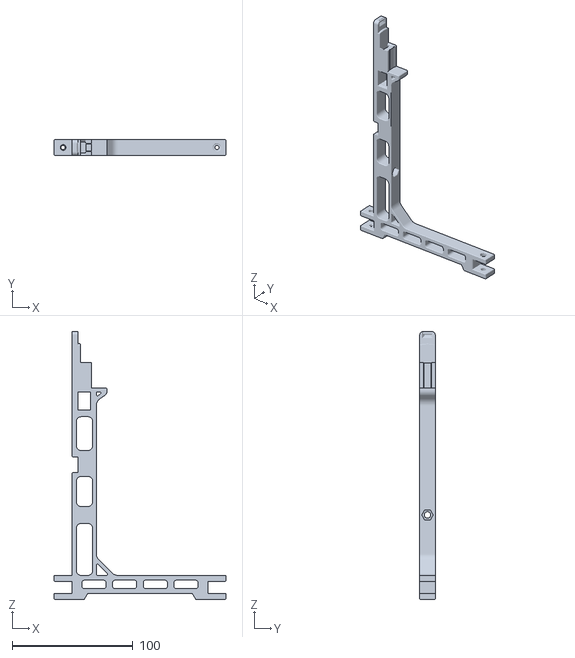
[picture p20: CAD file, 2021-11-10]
usermods/Carrot_Patch_ESUN_2.5kg/STL/Main_Body_ESUN_2.5kg.stl
142.4 x 13.0 x 222.0

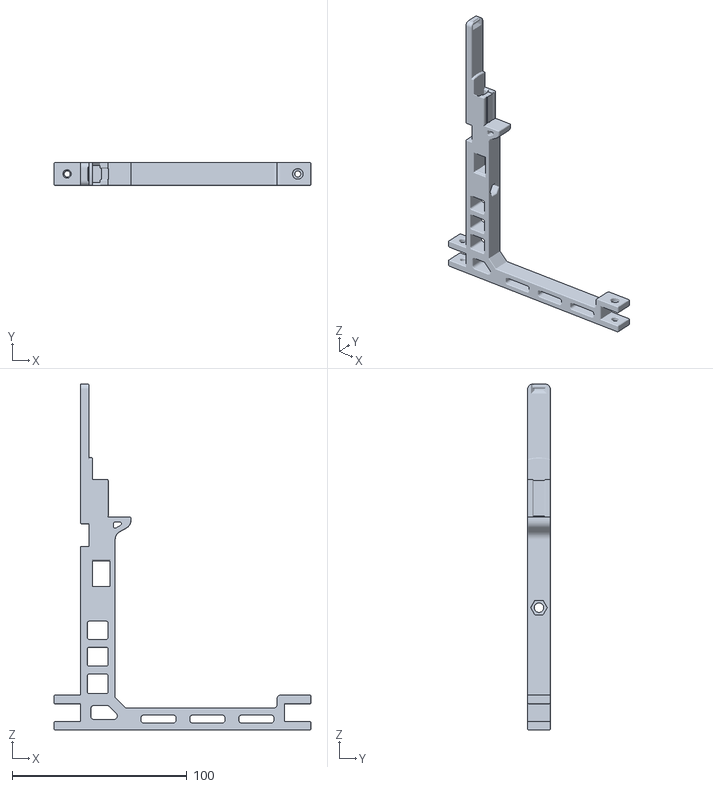
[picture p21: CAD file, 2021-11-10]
usermods/IKEA_Drybox_Carrot_Patch/STL/Main_Body_Drybox V1.1.stl
147.0 x 13.0 x 198.0

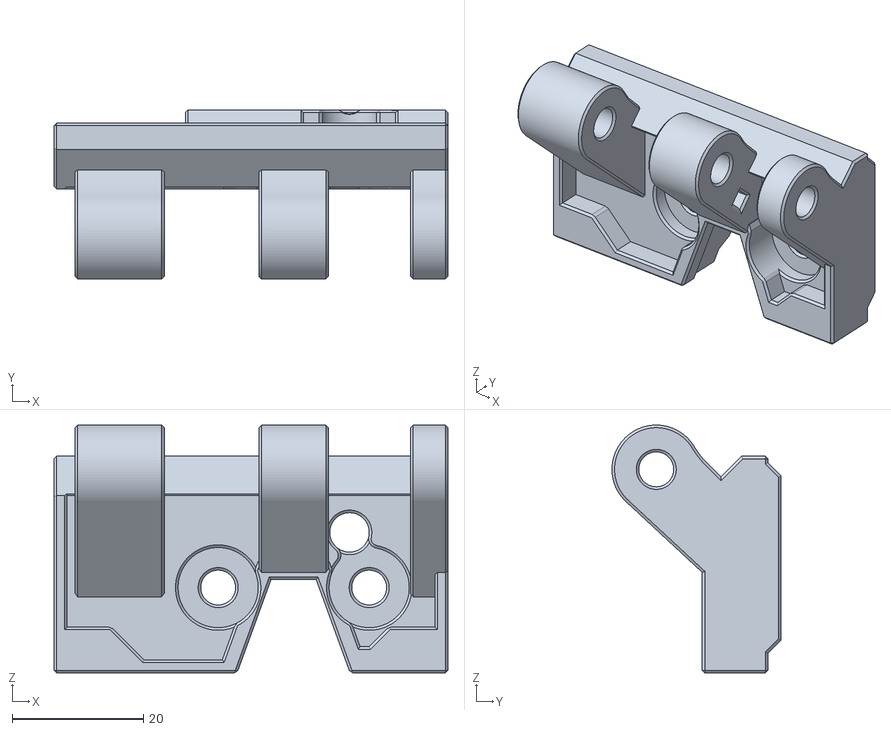
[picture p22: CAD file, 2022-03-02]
Carrot_Feeder/Stls/Filament blocks/Filament_Blocks_End.stl
60.0 x 25.7 x 37.7

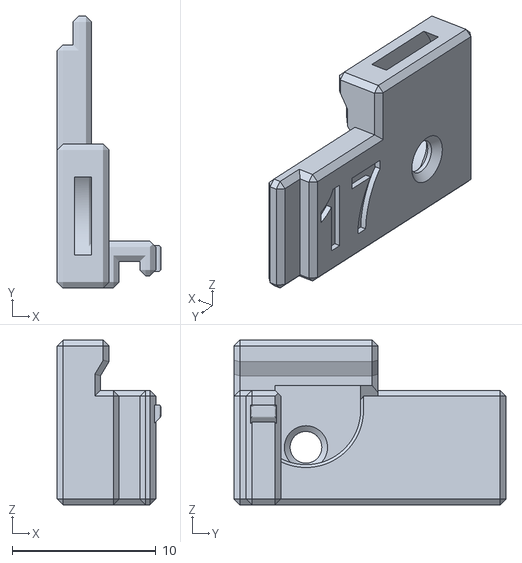
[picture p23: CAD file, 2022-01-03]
Carrot_Feeder/Stls/Filament blocks/Magnetic Gates/[a]_Magnetic_Gate_17.stl
7.20 x 18.9 x 11.5

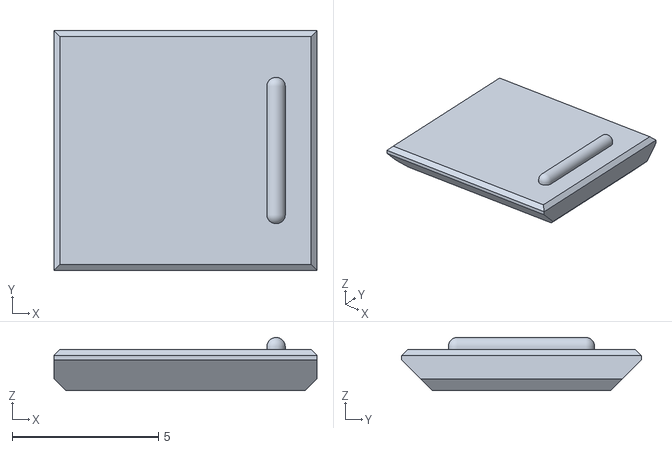
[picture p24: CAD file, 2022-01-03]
Carrot_Feeder/Stls/Filament blocks/MultiColor options/[MM]_Tag_Plate_10.stl
9.00 x 8.20 x 1.82

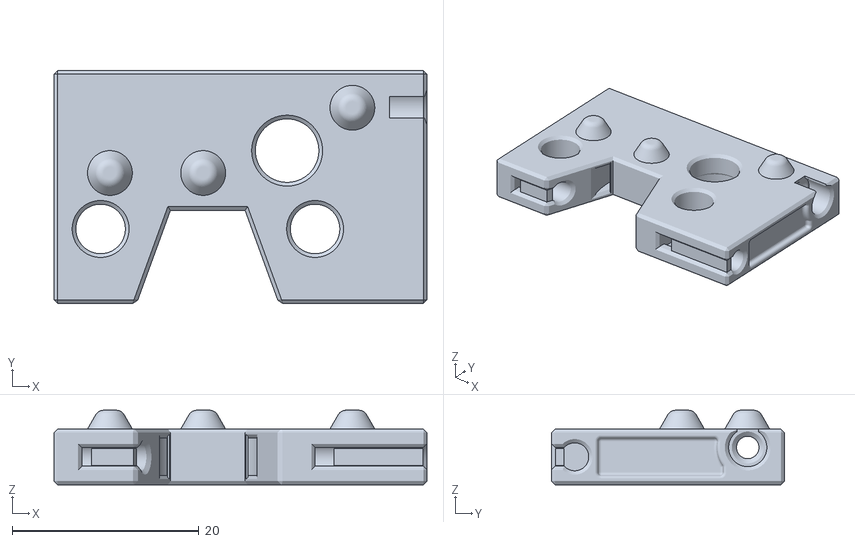
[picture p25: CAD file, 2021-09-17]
Carrot_Feeder/Stls/Filament blocks/Options/[a]_Bearing_Insert_Passthrough.stl
40.0 x 25.0 x 8.00

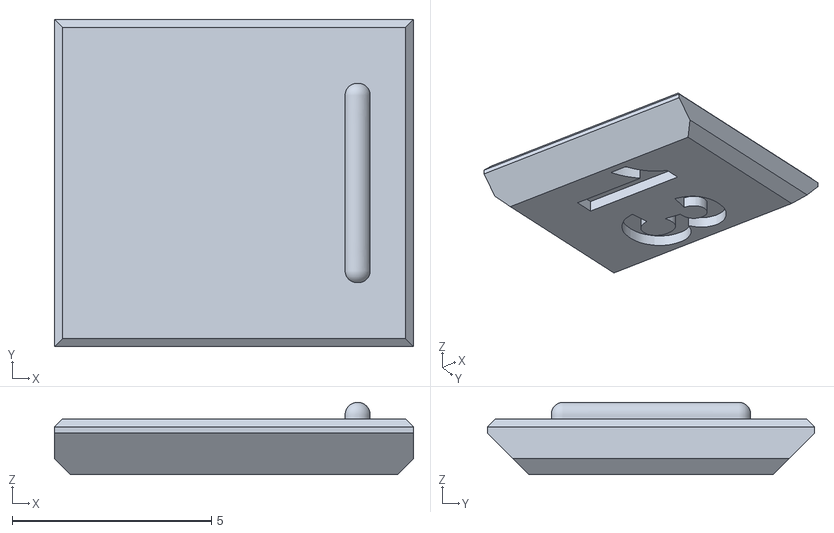
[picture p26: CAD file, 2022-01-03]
Carrot_Feeder/Stls/Filament blocks/Tag Plates/[a]_Tag_Plate_13.stl
9.00 x 8.20 x 1.82

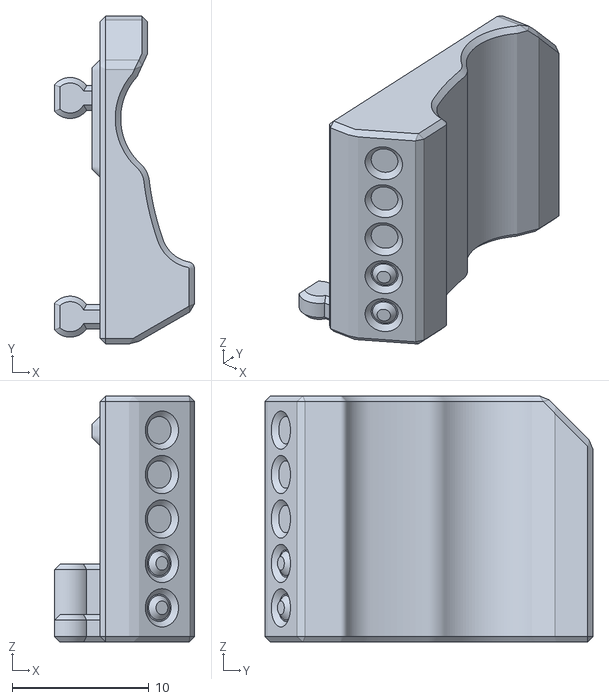
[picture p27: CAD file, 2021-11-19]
Carrot_Feeder/Stls/Filament blocks/Top Hat Lockers/Optionnal/Top_Hat_Locker_7_xN.stl
10.2 x 24.0 x 18.0

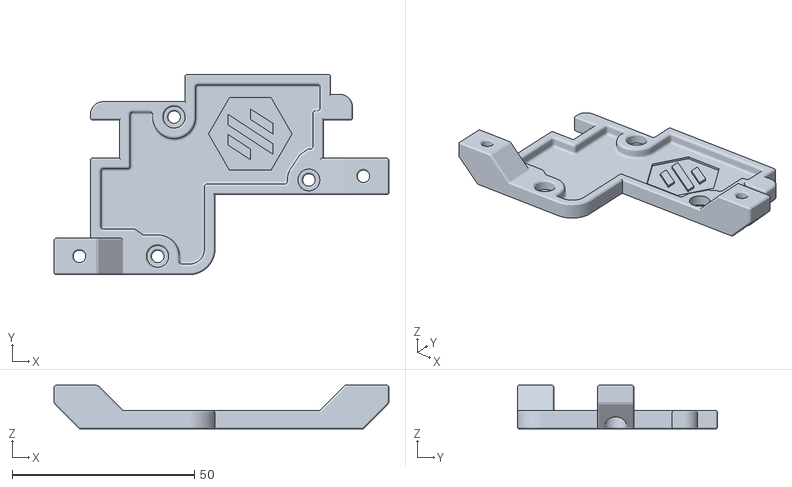
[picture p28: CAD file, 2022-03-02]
Carrot_Feeder/Stls/Gear box/[a]_Bottom_Panel.stl
92.0 x 55.0 x 12.0

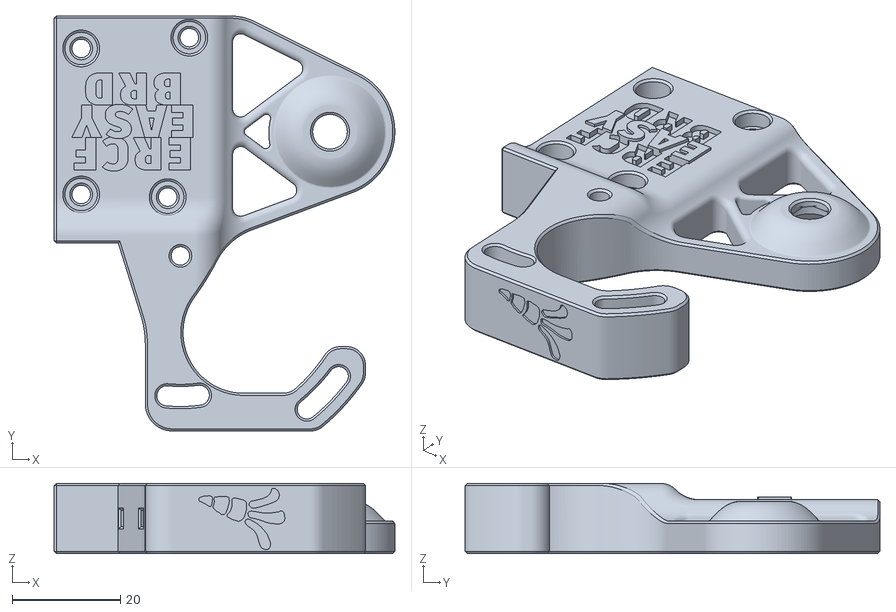
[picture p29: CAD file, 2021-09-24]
Carrot_Feeder/Stls/Gear box/EASY BRD Option/Motor_Arm_NEMA14_EASYBRD.stl
63.0 x 76.7 x 13.0

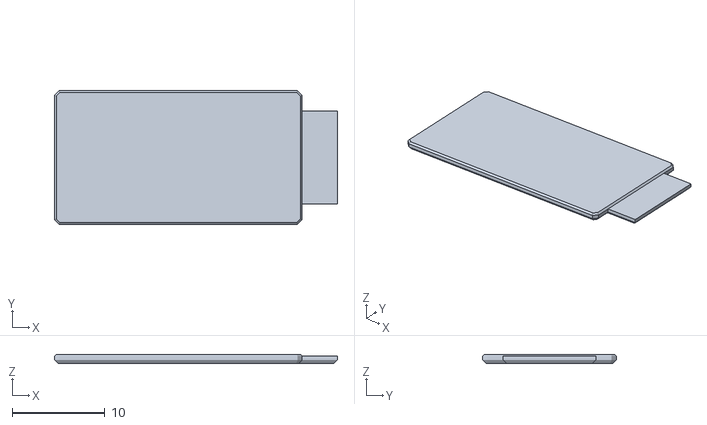
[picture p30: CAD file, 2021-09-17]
Carrot_Feeder/Stls/Gear box/MultiColor options/[MM]_Voron_Logo_Plate.stl
30.5 x 14.4 x 1.00

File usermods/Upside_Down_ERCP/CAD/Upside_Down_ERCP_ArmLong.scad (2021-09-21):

$fn=60;

vOffset = 3.5;

translate([-13,-2.5,14]) {
cube([5,5,10]);
}

translate([-12.5,-6.5,21.65]) {
cube([15,13,1]);
}

translate([-3,-6.5,18.65]) {
cube([5,13,3]);
}

difference() {
union () {
difference () {
translate([0,-6.5,0]) {
import("../../../Carrot_Patch/STLs/Spool_Arm_Long.stl");
}

translate([-13,0,10]) {
rotate([0,90,0]) {
    cylinder(d=4.5,h=4.3);
}
}


translate([0,-10,0]) {
cube([150,20,30]);
}
}

translate([0,-6.5,0]) {

//cube([4,13,12]);
}
difference() {
    translate([0,0,29+vOffset]) {
rotate([180,0,0]) {
difference() {
translate([0,-6.5,0]) {
import("../../../Carrot_Patch/STLs/Spool_Arm_Long.stl");
}
translate([-20,-10,0]) {
cube([20,20,40]);
}
}
}
}
translate([0,-10,-10]) {
cube([250,20,10]);
}

}
}


translate([-7,0,8.25+vOffset]) {
rotate([0,90,0]) {
cylinder(d=4.3,h=120);
}
}

translate([0,-6.5,0]) {
translate([0,0,0]) {
cube([75,13,8]);
}
}


translate([-15,-10,32.5]) {
cube([20,20,20]);
}

translate([-10,-8,22.65]) {
cube([5,5,20]);
}

translate([-10,3,22.65]) {
cube([5,5,20]);
}

}

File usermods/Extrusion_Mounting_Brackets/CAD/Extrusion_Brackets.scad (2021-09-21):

$fn = 30;

// The width of the border in mm
borderWidth = 5;

// The spacing between the mounting holes
// 78 for the ERCF v1.0, 101.172 for the ERCP v1.1
holeSpacing = 101.172;

// The size of the extrusions (only square supported)
extrusionSize = 20;

// Calculates the spacing between both extrusions
extrusionSpacing = holeSpacing - 20;

difference()
    {
        // Bigger outside cube
        cube([ extrusionSize + borderWidth,
               extrusionSize * 2 + extrusionSpacing + borderWidth * 2,
               extrusionSize + borderWidth ]);

        // Smaller inside cube
        translate([borderWidth, borderWidth, borderWidth])
        {
            cube([ extrusionSize,
                   extrusionSize * 2 + extrusionSpacing,
                   extrusionSize ]);
        }

        // Left screw hole, parallel to the extrusion
        translate([ 0,
                    extrusionSize / 2 + borderWidth,
                    extrusionSize / 2 + borderWidth])
        {
            rotate([0, 90, 0])
            {
                cylinder(d = 5.5, h = borderWidth);
            }
        }

        // Left screw hole, perpendicular to the extrusion
        
        translate([ extrusionSize / 2 + borderWidth,
                    0,
                    extrusionSize / 2 + borderWidth])
        {
            rotate([0, 90, 90])
            {
                cylinder(d = 5.5, h = borderWidth);
            }
        }


        // Right screw hole, parallel to the extrusion
        translate([ 0,
                    extrusionSize / 2 + borderWidth + extrusionSpacing + extrusionSize,
                    extrusionSize / 2 + borderWidth])
        {
            rotate([0, 90, 0])
            {
                cylinder(d = 5.5, h = borderWidth);
            }

        }
        
        // Right screw hole, perpendicular to the extrusion
        translate([ extrusionSize / 2 + borderWidth,
                    extrusionSize + borderWidth + extrusionSpacing + extrusionSize,
                    extrusionSize / 2 + borderWidth])
        {
            rotate([0, 90, 90])
            {
                cylinder(d = 5.5, h = borderWidth);
            }

        }
        
        // Left screw hole, bottom of the extrusion
        translate([ extrusionSize / 2 + borderWidth,
                    extrusionSize / 2 + borderWidth,
                    0
                    ])
        {
            rotate([0, 0, 0])
            {
                cylinder(d = 5.5, h = borderWidth);
            }
        }

        // Right screw hole, bottom of the extrusion
        translate([ extrusionSize / 2 + borderWidth,
                    extrusionSize / 2 + borderWidth + extrusionSpacing + extrusionSize,
                    0])
        {
            rotate([0, 0, 0])
            {
                cylinder(d = 5.5, h = borderWidth);
            }
        }
    }
        

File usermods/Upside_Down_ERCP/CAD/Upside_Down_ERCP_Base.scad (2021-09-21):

$fn=30;

difference () {
translate([4,-2.82,2.5]) {
import("../../../Carrot_Patch/STLs/Main_Body.stl");
}

translate([-16,10,0]) {
rotate([0,90,0]) {
cylinder(d=3.3,h=7);
}
}

translate([-16,10,0]) {
rotate([0,90,0]) {
cylinder(d=6,h=3);
}
}
translate([4,-20,-10]) {
cube([20,20,20]);
}
}

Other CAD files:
usermods/CW2_with_ECAS_and_optional_sensor/STL/main_body_with_ECAS.stl
usermods/CW2_with_ECAS_and_optional_sensor/STL/main_body_with_ECAS_and_sensor.stl
Carrot_Feeder/Stls/Filament blocks/Top Hat Lockers/Top_Hat_Locker_5_xN.stl
usermods/Upside_Down_ERCP/CAD/Upside_Down_ERCP_ArmShort.scad
Carrot_Feeder/Stls/Filament blocks/Filament_Block_xN.stl
Carrot_Feeder/Stls/Filament blocks/Magnetic Gates/[a]_Magnetic_Gate_0.stl
Carrot_Feeder/Stls/Filament blocks/Magnetic Gates/[a]_Magnetic_Gate_1.stl
Carrot_Feeder/Stls/Filament blocks/Magnetic Gates/[a]_Magnetic_Gate_10.stl
Carrot_Feeder/Stls/Filament blocks/Magnetic Gates/[a]_Magnetic_Gate_11.stl
Carrot_Feeder/Stls/Filament blocks/Magnetic Gates/[a]_Magnetic_Gate_12.stl
Carrot_Feeder/Stls/Filament blocks/Magnetic Gates/[a]_Magnetic_Gate_13.stl
Carrot_Feeder/Stls/Filament blocks/Magnetic Gates/[a]_Magnetic_Gate_14.stl
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

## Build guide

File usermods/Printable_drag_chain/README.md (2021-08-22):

# ERCF Printable Drag Chain

A printable cable chain suitable for use with the [Enraged Rabbit Carrot Feeder][ercf], but the design is fully parametric so it can be resized to fit many applications.

ERCF with 3D printed drag chain

The link design is taken from Thingiverse ["Yet Another Parametric Drag Chain"][thing] by **destroyer2012** and is licensed under Creative Commons CC-A (attribution required).

The two end links are original work, copyright © 2021 Timothy P. Long and licensed under the [Tigra MIT license][mit].

The Fusion 360 CAD model is included. The design is fully parametric so you can resize it how you like. The model is configured by default to be appropriate for use with ERCF (7x7mm internal size with mounting holes 10mm on centers).

## Printing Recommendations

Use your own discretion and experience, but as a staring point, we suggest:

- 0.4mm nozzle, 0.2mm layer height
- ABS or PETG. PLA _**not** recommended_ because it tends to creep over time and we have had a lot of problems with PLA cable chains falling apart after a few weeks.

For a 5-position ERCF, you need one of each end link and 13 mid links. We haven't measured other sizes.

Support material needed for printing is included in the model, there is no need to add any in the slicer. For this to work correctly, the correct orientation on the build plate must be used.

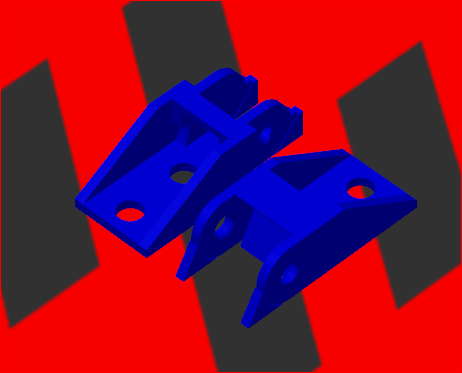
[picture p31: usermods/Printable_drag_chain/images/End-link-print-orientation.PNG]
End link orientation

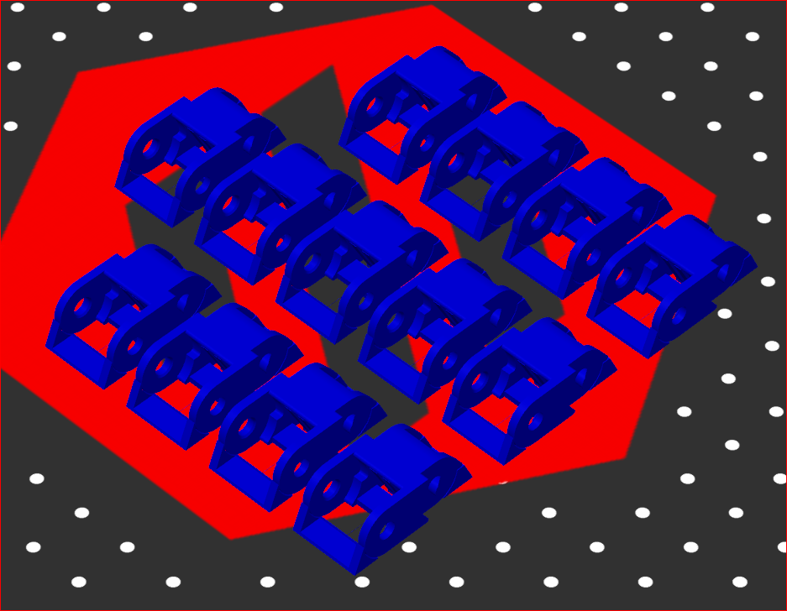
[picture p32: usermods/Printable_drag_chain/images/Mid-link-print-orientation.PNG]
Mid link orientation


[thing]: https://www.thingiverse.com/thing:4598740 "Thingiverse thing:4598740"
[mit]: https://tigra.mit-license.org "Tigra MIT License"
[ercf]: https://github.com/EtteGit/EnragedRabbitProject "Enraged Rabbit Project"

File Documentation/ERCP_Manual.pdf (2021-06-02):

# Enraged Rabbit Project

# Carrot Patch V1.1 assembly

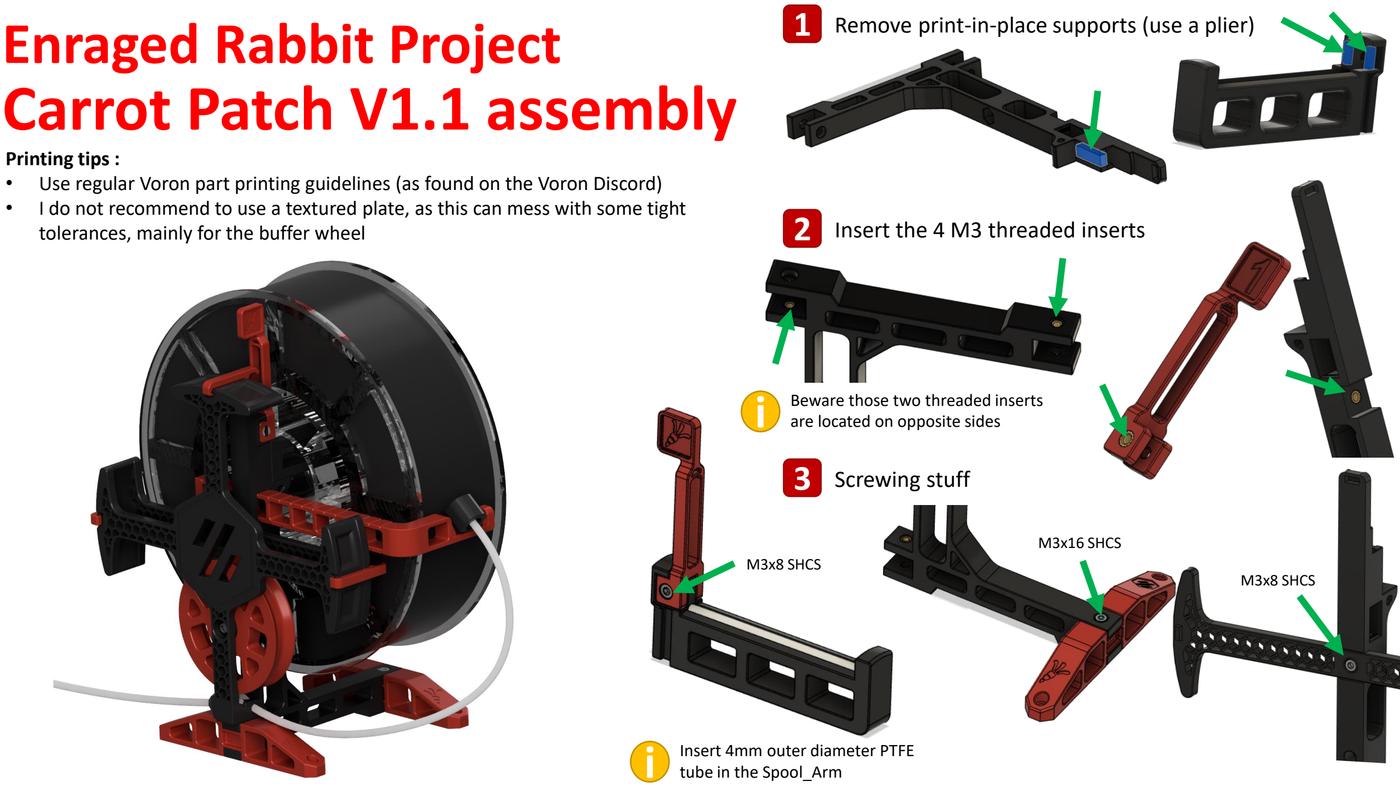
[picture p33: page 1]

## 1 Remove print-in-place supports (use a plier)

## 2 Insert the 4 M3 threaded inserts

## 3 Screwing stuff

M3x16 SHCS
M3x8 SHCS
M3x8 SHCS

Printing tips :
- Use regular Voron part printing guidelines (as found on the Voron Discord)
- I do not recommend to use a textured plate, as this can mess with some tight tolerances, mainly for the buffer wheel

Beware those two threaded inserts i are located on opposite sides

Insert 4mm outer diameter PTFE i tube in the Spool_Arm

## 4 Wheel and buffer assembly

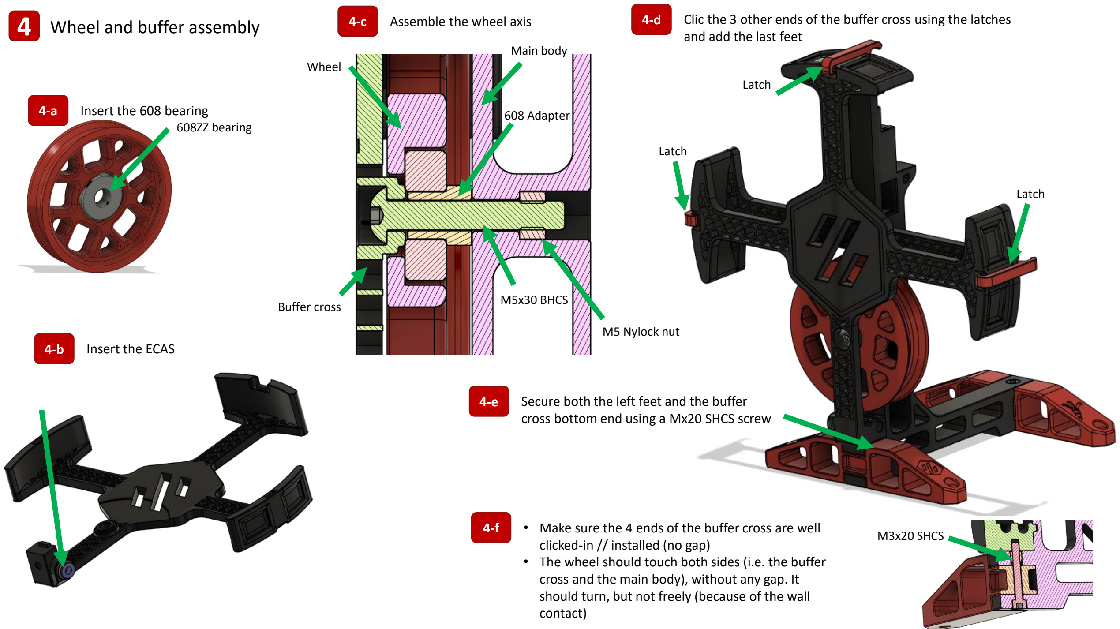
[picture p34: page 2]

608ZZ bearing

Wheel

Main body

M5 Nylock nut

M5x30 BHCS

608 Adapter

Buffer cross

Latch

Latch

Latch

4-b | Insert the ECAS
4-a | Insert the 608 bearing
4-e | Secure both the left feet and the buffer cross bottom end using a Mx20 SHCS screw
4-d | Clic the 3 other ends of the buffer cross using the latches and add the last feet
4-f | • Make sure the 4 ends of the buffer cross are well clicked-in // installed (no gap) • The wheel should touch both sides (i.e. the buffer cross and the main body), without any gap. It should turn, but not freely (because of the wall contact)
4-c | Assemble the wheel axis

M3x20 SHCS

## 5 Sliding arm

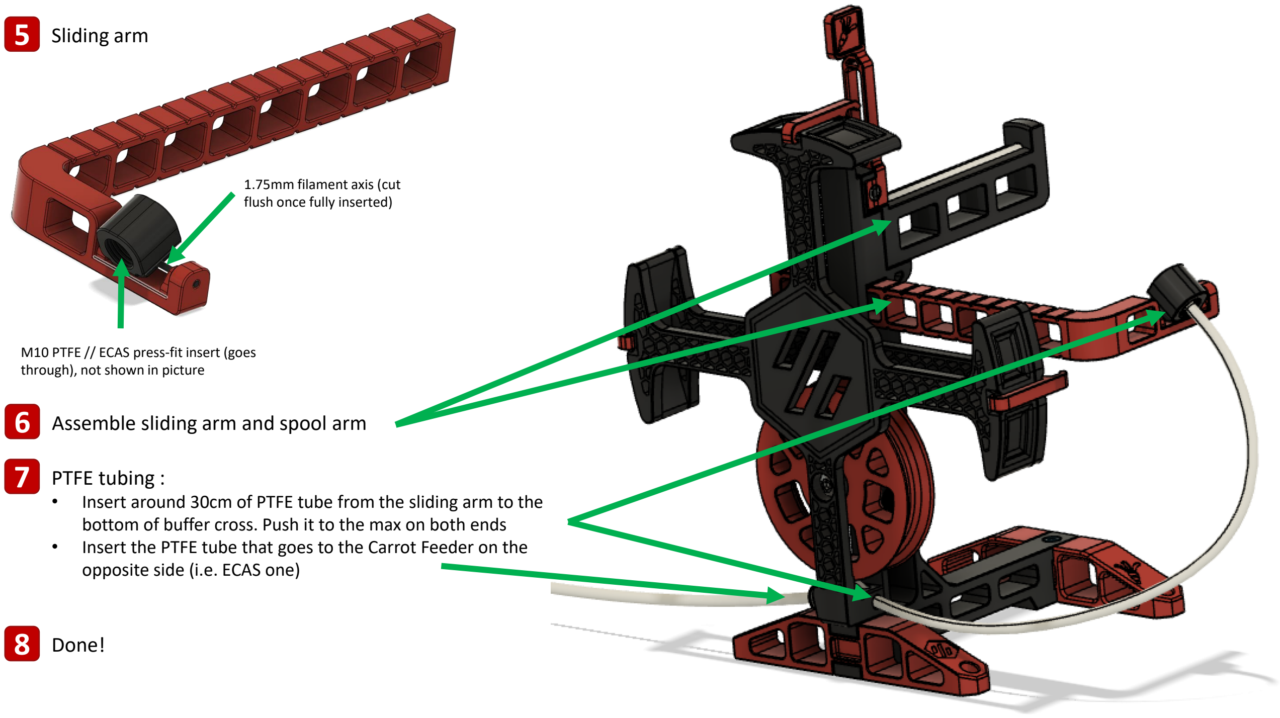
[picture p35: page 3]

## 6 Assemble sliding arm and spool arm

1.75mm filament axis (cut
flush once fully inserted)

M10 PTFE // ECAS press-fit insert (goes
through), not shown in picture

## 7 PTFE tubing :

- Insert around 30cm of PTFE tube from the sliding arm to the bottom of buffer cross. Push it to the max on both ends
- Insert the PTFE tube that goes to the Carrot Feeder on the opposite side (i.e. ECAS one)

## 8 Done!

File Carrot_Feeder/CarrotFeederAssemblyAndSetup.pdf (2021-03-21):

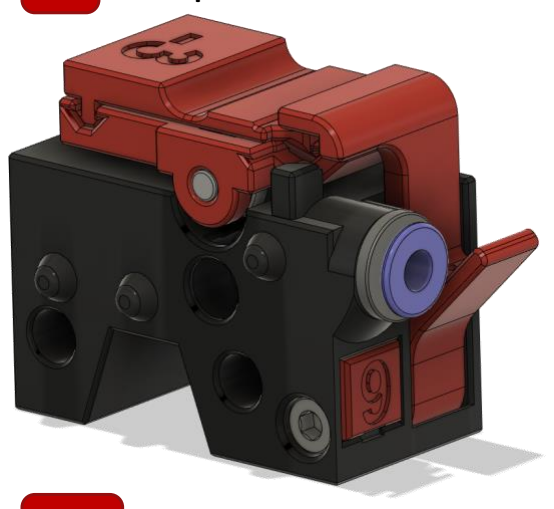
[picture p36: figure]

Every 6x3 magnet insert on the Carrot Feeder has a small flat slot on the i side : use it to easily remove the magnet if needed

# Enraged Rabbit Project

# Carrot Feeder assembly and setup

## 1 Prepare the filament blocks

Printing tips :
- Use the printing tips found on the EnragedRabbit Github (Carrot Feeder section)
- Each channel of the Carrot Feeder is one filament block
- There two available versions for the block : with or without the M3 threaded insert. The threaded insert is though to insert properly, so if you’re not comfortable doing it, use the

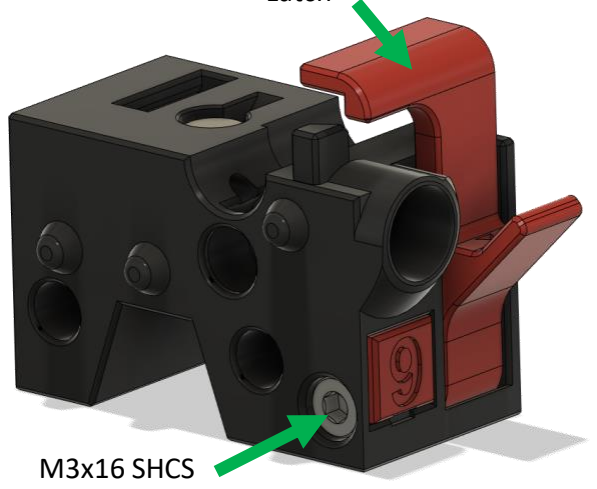
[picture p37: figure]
M3x16 SHCS

version without it (you’ll screw the M3x16 directly in the plastic)

1-a Insert the magnet and the M3 threaded insert

6x3 magnet

1-b Insert the latch, lock it with the M3x16 screw (don’t screw too hard, be gentle) and insert the numbering plate (just click it in)

Latch

Numbering plates can be easily removed with a small flat-head screwdriver, i using the bottom slot of the plate

1-c Prepare the filament block top hat

- Install the free rolling bondtech gear, take care of its orientation!
- Insert the 6x3 magnet : IT SHOULD REPEL THE ONE FROM THE FILAMENT BLOCK

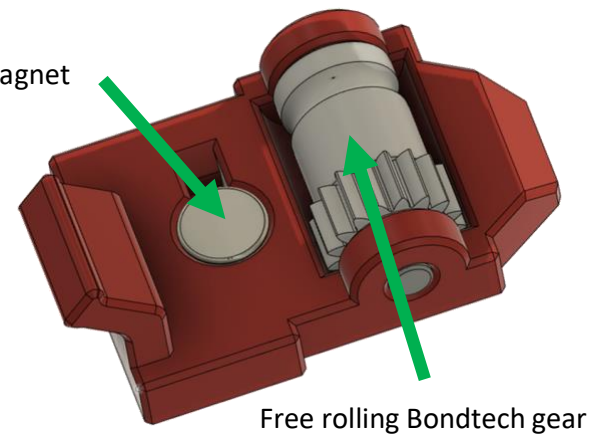
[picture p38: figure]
Free rolling Bondtech gear

| 6x3 magnet
1-d | Slide in the top hat locker plate (use the « 0 » value to begin with). Make sure it’s fully inserted
1-e | Press-fit the ECAS bowden fit and install the top hat block you just did

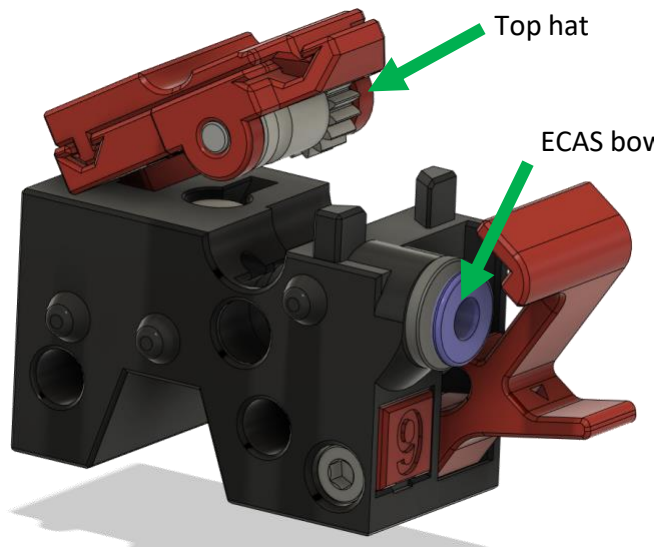
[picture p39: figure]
Top hat

ECAS bowden fitting

- Top hat should be inserted without forcing too much (play with the part orientation)
- Once inserted, rest position should be as seen on the left, thanks to the repelling magnets (with latch open)
- Push down the top hat and close the latch. You can now press on the top hat with a finger (it will go down) and release the finger (it will go up), like a spring mechanism

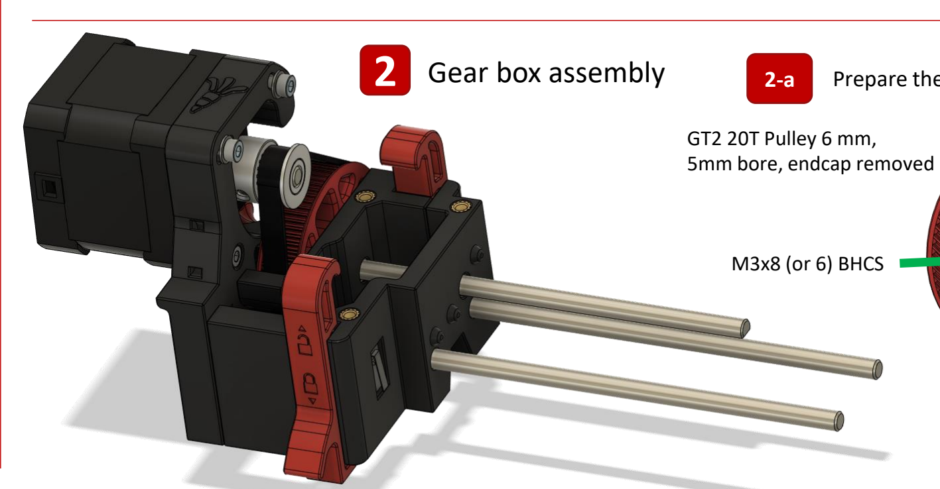
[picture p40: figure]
M3x8 (or 6) BHCS; GT2 20T Pulley 6 mm, 5mm bore, endcap removed

2 Gear box assembly | 2-a | Prepare the M4 wheel

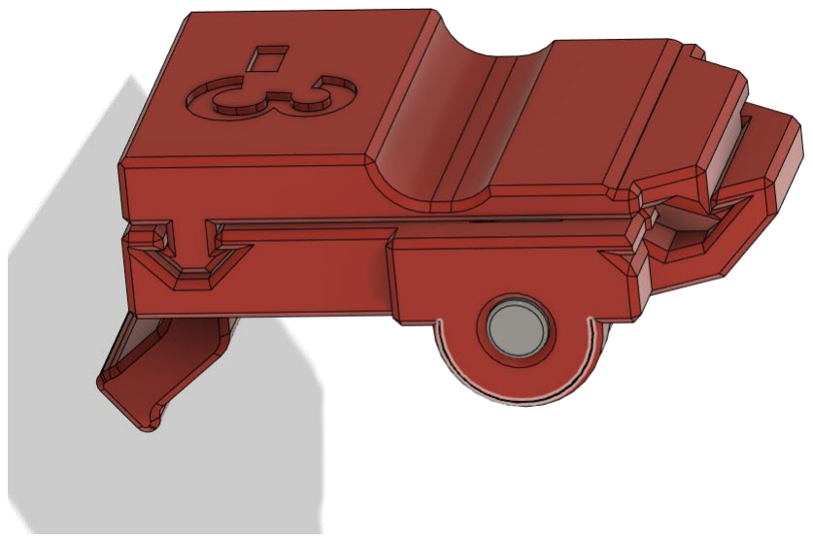
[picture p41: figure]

- Those M3 threaded inserts are difficult to insert (not much

plastic behind), go slowly and do not put your soldering iron tip inside the insert if the tip sticks out of it
- Push those inserts using the soldering iron from the side, and

take your time to make them well aligned with the holes

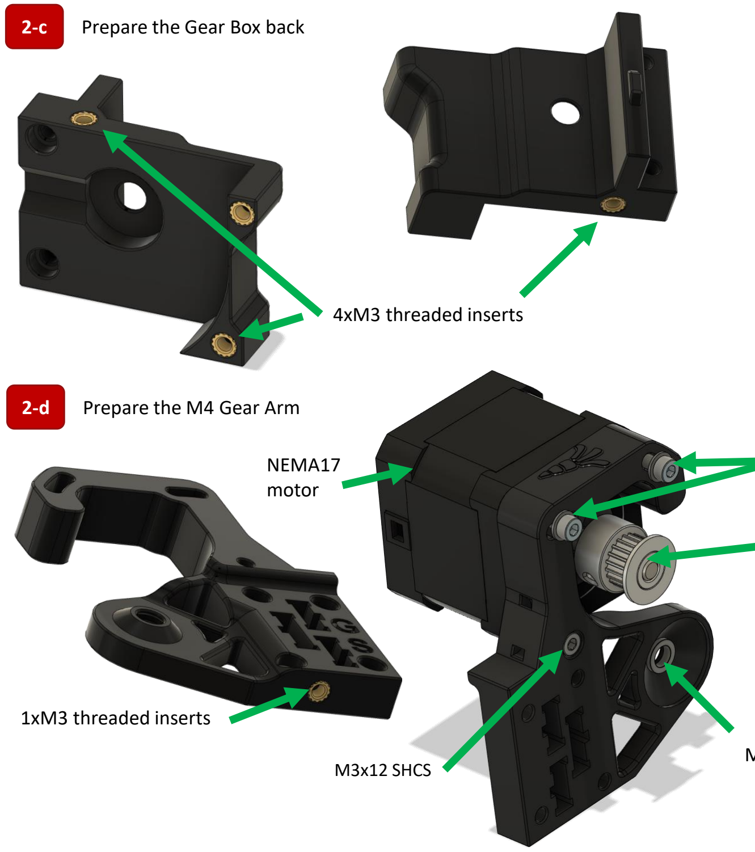
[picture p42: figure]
Prepare the Gear Box back; 4xM3 threaded inserts; 1xM3 threaded inserts; Prepare the M4 Gear Arm; NEMA17 motor; M3x12 SHCS

MR85 bearing

GT2 20T
Pulley 6 mm,
5mm bore

M3x16 SHCS
+ M3 Washer

Don’t forget to put some blue Loctite or similar on the grub screw of the GT2 20T Pulley

- Pre-wire the mechanical endstop (should be in a NO configuration). Prepare around 10 cm long of cables (24 awg is more than enough). Crimping

2-e | Prepare the 2x M5 threaded rods
| 2xM5 nuts (nut + counter- nut) OR 1xM5 nut + 1xM5 Nylock nut (the outside one)
- You can already install the Gear motor (G label on the connector plate) cabling. Connect the 4 pins molex microfit connector in the dedicated slot (press fit). Use the zip-tie channel to secure the cable path

Zip tie channel

Gear motor
connector slot

The microfit connector to install in the ERCF is the Female housing (with i Male crimps). Just push them from the ERCF inside towards the exterior

Molex Microfit
connector to
install in the
ERCF part
2-f | Install the threaded rods in the Gear Box Front
2-g | Install the first Side Latch and the Gear Box Back

2x M3x20 SHCS

Before installing the Side Latches, make sure you’ve released their print-in-place mechanism (use a allen wrench in the arm’s hole to unlock it if needed)

i

- Do not screw too hard the 2x M3x20 SHCS, you should be able to lock//unlock the latch without trouble

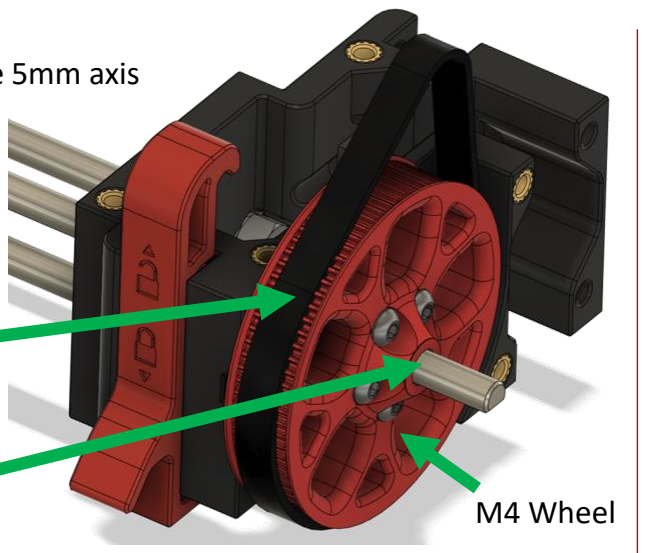
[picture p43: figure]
M4 Wheel

2-g Install the 5mm axis

No need to tighten the grub screws for the M4 wheel i yet, we’ll adjust the wheel//shaft position later

5mm D-cut shaft

188mm GT2,
6mm belt

Don’t forget to install the belt!

2-h | Install the 2nd Side Latch and the M4 Gear Arm

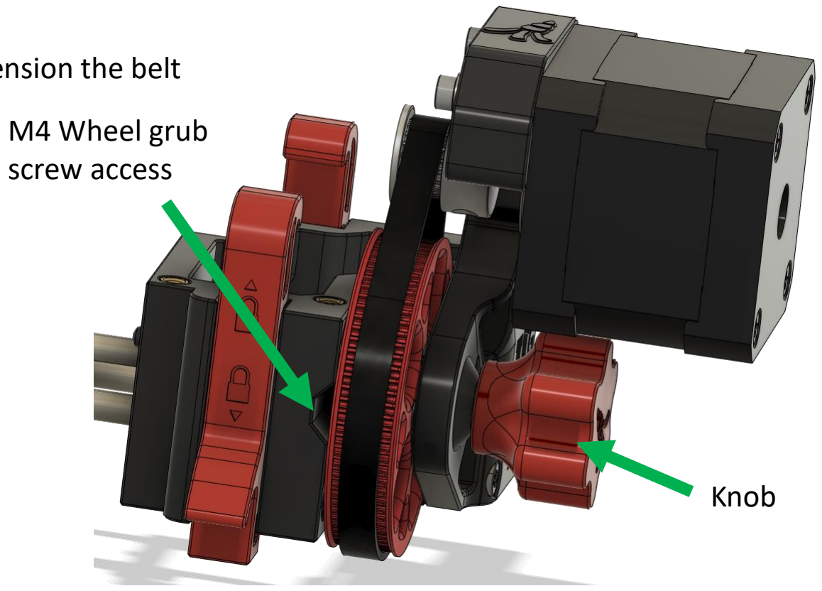
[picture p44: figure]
Knob; M4 Wheel grub screw access

2-i | Install the knob, tighten the M4 grub screw and tension the belt
- Press fit to the max the Knob on the 5mm shaft
- Put the Knob + Shaft assembly at around 1mm of the M4 Gear Arm part
- Tighten the M4 Wheel grub screws using the side access
- Tighten the belt by rotatin the motor around it’s M3x12 SHCS screw
- Test the motion using the Knob, it should be smooth
2-j | Take a break, eat some gummy bears (not provided) or whatever, if you want !
4-a | Slide a single Bondtech gears on the

4-b Slide in the first filament block

Filament Block

4-c | Repeat steps 4-a and 4-b for all your Filament Blocks

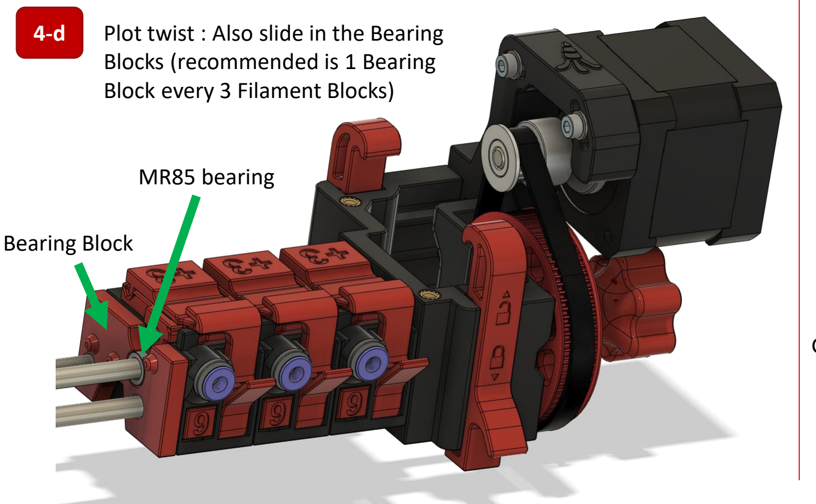
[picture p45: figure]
Blocks (recommended is 1 Bearing Block every 3 Filament Blocks); MR85 bearing; Bearing Block

4-d | Plot twist : Also slide in the Bearing
4-e | When all blocks are inserted, install the Block End

M5 washer + Nut (not shown yet)

- Use your fingers to push the threaded rods, in the gear box, into their proper position
- Tighten the M5 nuts on the M5 threaded rods
- While the whole assembly should be relatively stiff, it will flex//bend, this is expected
- Check that the 5mm D-cut shaft is well inserted into the bearing of the Block End
- Don’t check the 5mm axis motion yet, as no Bondtech gears are tighten yet

## 5 Align and tighten the Bondtech gears

- Use a small ptfe tube (a few cms long is enough) and insert it in the first channel
- Use a some 1,75mm filament and insert it in the channel
- Use the knob to align the D-Cut shaft (cut facing the top)
- Align the Bondtech gears properly on the filament and screw it down, use some blue Loctite on the grub screw
- To check the proper alignement : Once done, let the filament in the filament block and turns by hand the gear axis using the knob (both directions). The filament should not move (it should not touch the Bondtech gears you’ve just fixed)
- Repeat this process for all channels

Gear to align

1,75mm
filament

## 6 Assemble the detector cart

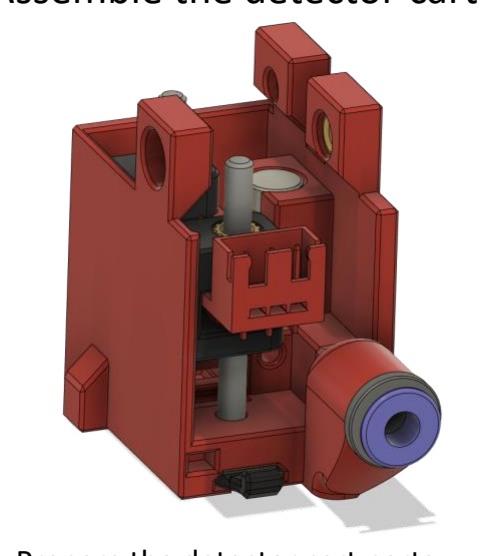
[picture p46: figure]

6-a | Prepare the detector cart parts
6-b | Install the lever

1,75mm axis (not shown)

- Make sure the lever spins freely around the 1,75mm filament axis
- Install the magnets so they repel each other !
- The rest position of the lever should be
« down » (right picture) while the triggered position (using a 1,75 filament) should be
« up » (left picture)

Rest position

Triggered position

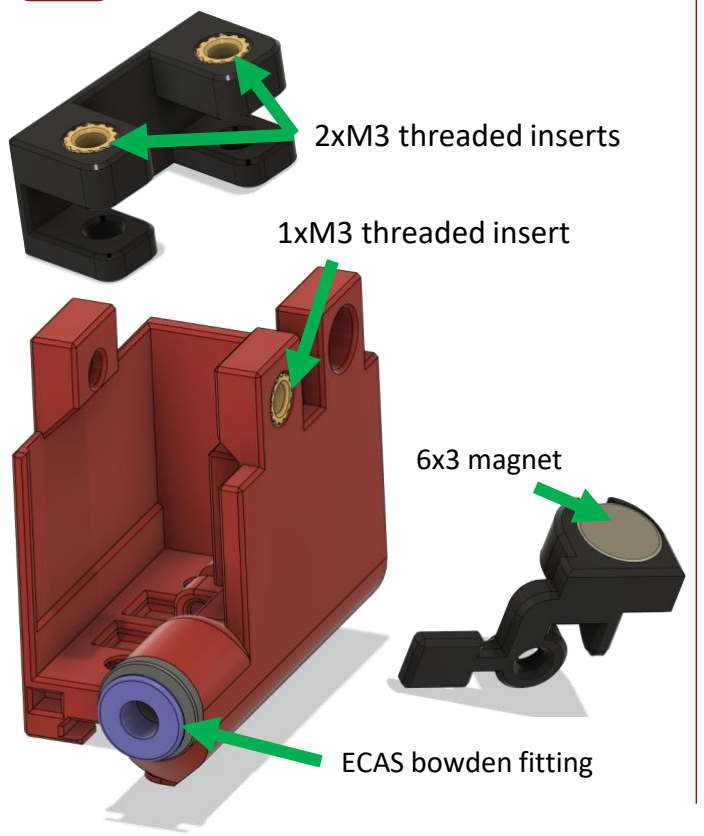
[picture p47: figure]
2xM3 threaded inserts; 1xM3 threaded insert; 6x3 magnet; ECAS bowden fitting

6-c Install the optical detector

2x M3x30 SHCS

- Slide the optical detector into its support
- Install the detector support in the detector cart and

then slide//screw in the 2xM3x30 SHCS screws
- Use the screws to position the detector around the middle of his allow movement range
- Make sure the head of the 2 screws are well inserted in the bottom slots of the detector cart and then slide in the Sliding Locker

Optical detector

Sliding Locker

You can now use the two screws to precisely adjust the optical detector position (we’ll do that later in the assembly//setup)

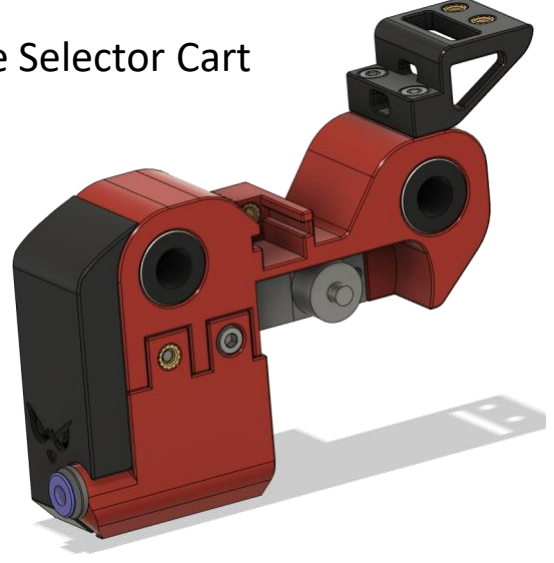
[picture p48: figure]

## 7 Assemble the Selector Cart

7-a Prepare the detector cart parts

- Make sure magnets (Selector Cart and the Selector Door) attract each other
- Use 2x M2x8mm screws (or similar) to fix the servo on the cart, directly screw in the plastic part
- The LM8UU (or the RJ4JP-01-08) are press-fitted in their slot

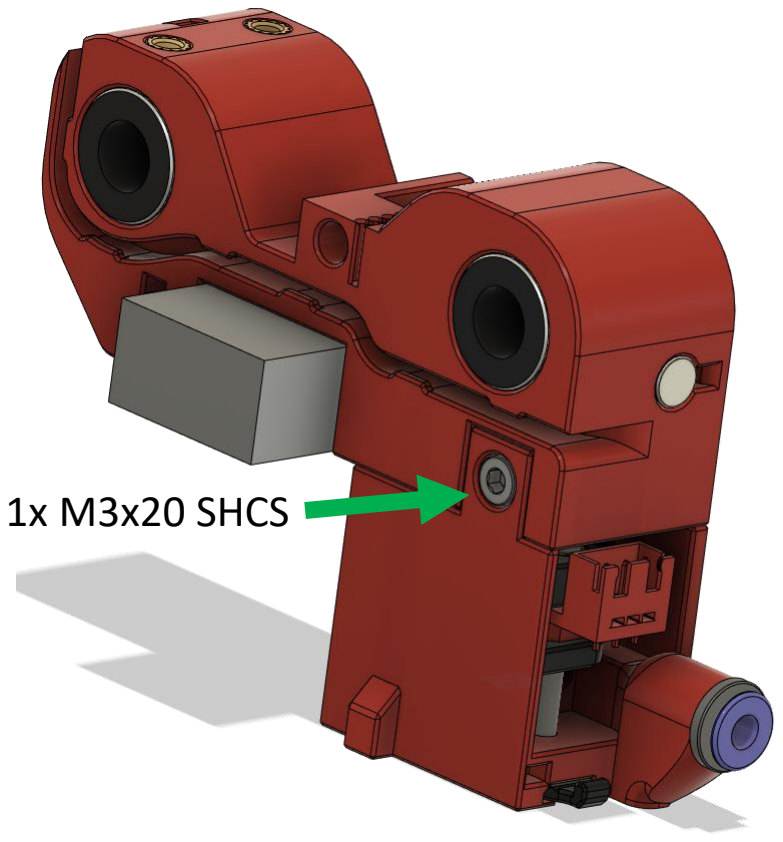
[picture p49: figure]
1x M3x20 SHCS

- Slide-in the Detector Cart, make sure the 2x M3X20 SHCS screws of the Detector Cart slides properly in their dedicated slots on the Selector Cart (they are not screwed-in, just guided)
- Just clip the door, as shown on the item #7. We’ll deal with the wiring later on

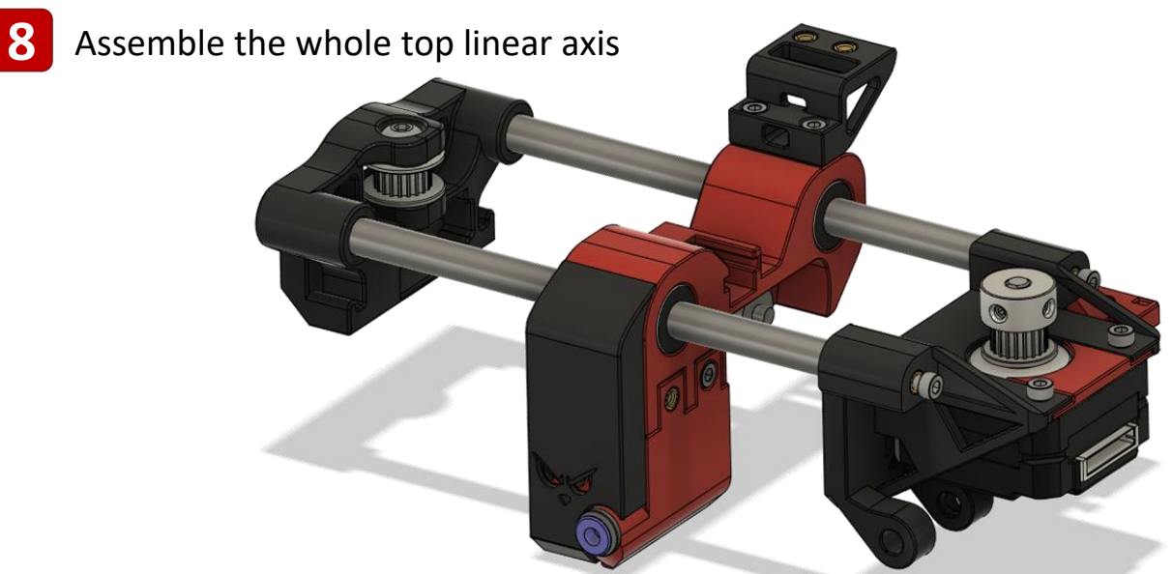
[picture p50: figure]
8 Assemble the whole top linear axis

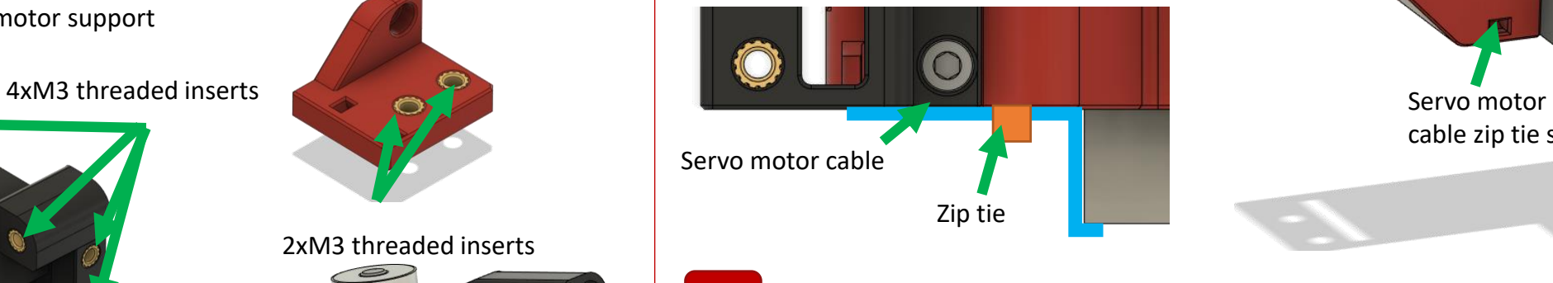
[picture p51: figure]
4xM3 threaded inserts; Servo motor; 2xM3 threaded inserts; Servo motor cable; Zip tie
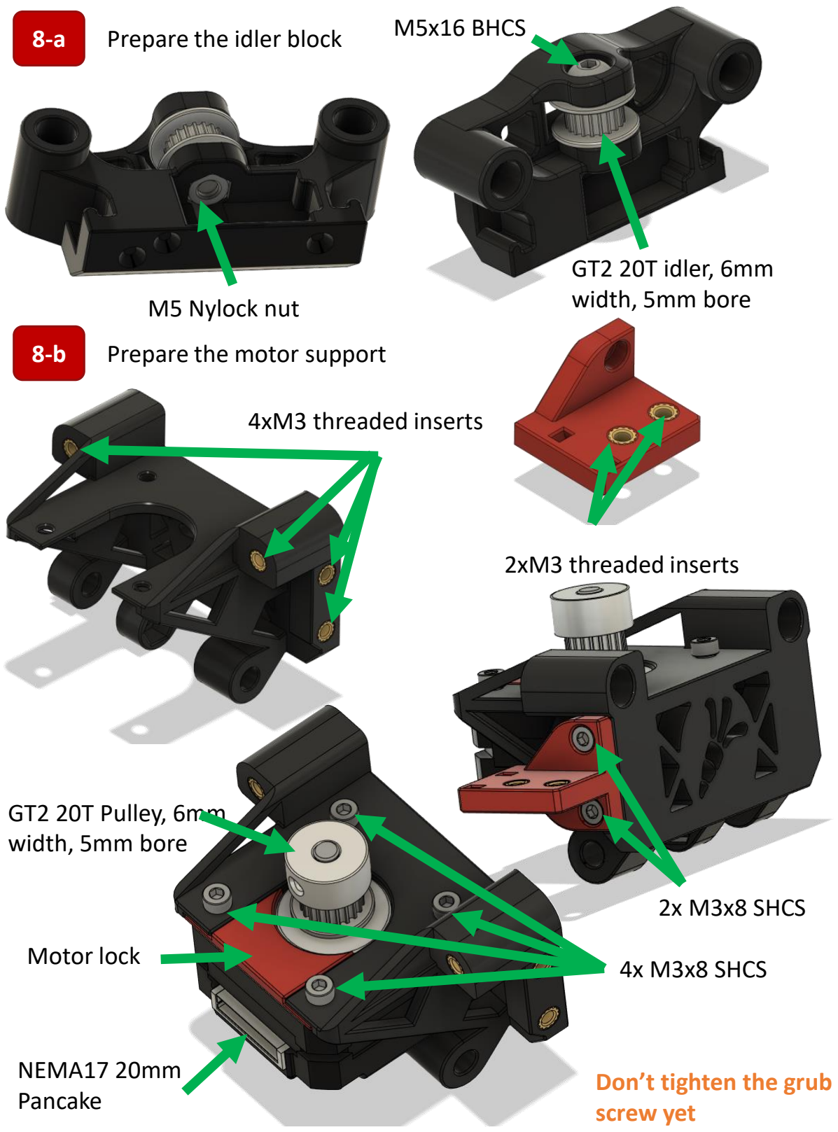
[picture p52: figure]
Prepare the idler block; M5x16 BHCS; GT2 20T idler, 6mm; width, 5mm bore Nylock nut; Prepare the motor support; 2x M3x8 SHCS; 4x M3x8 SHCS Motor lock; GT2 20T Pulley, 6mm width, 5mm bore; NEMA17 20mm Pancake; Don’t tighten the grub screw yet

8-d Assemble the axis

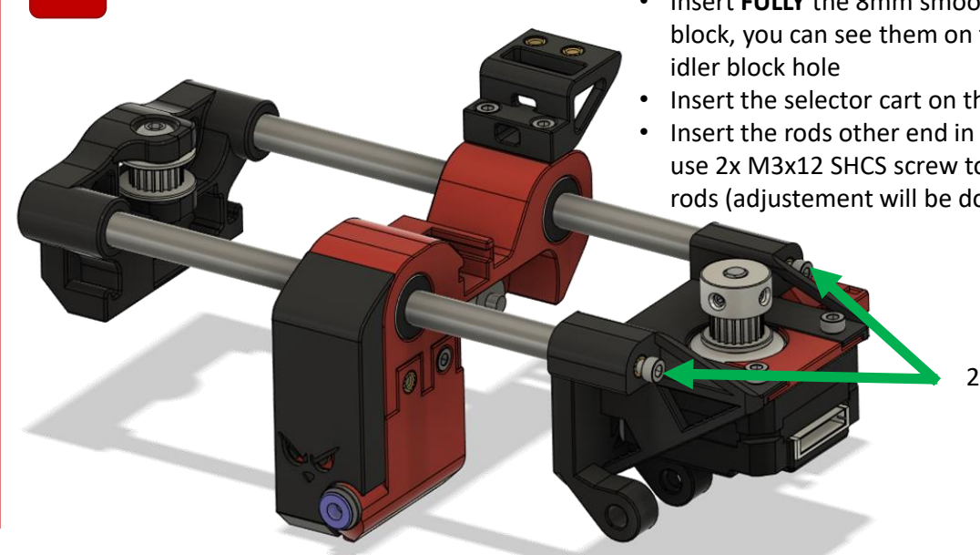
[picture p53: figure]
idler block hole

2x M3x12 SHCS

- Insert FULLY the 8mm smooth rods in the idler block, you can see them on the other side of the
- Insert the selector cart on the 8mm rods
- Insert the rods other end in the motor support, and use 2x M3x12 SHCS screw to get in contact with the rods (adjustement will be done later on)

8-c Prepare the selector cart cabling

- Connect the optical sensor using a JST connector and then insert the 3 wires into the dedicated groove, up to the drag chain anchor point
- Use the servo motor cable zip tie slot to firmly secure the servo wiring, make sure the servo cable is doing a nice « 90° » turn in between the servo and the zip tie slot, as shown below

## 9 Assemble the top block to the bottom one

- Tighten the 2x M5x30 BHCS screws

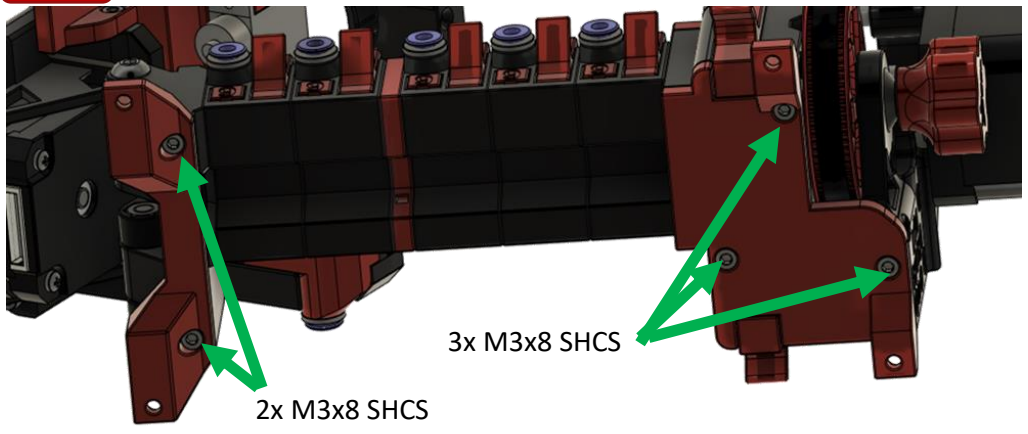
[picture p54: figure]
2x M3x8 SHCS; 3x M3x8 SHCS

- Pass the servo and optical sensors cables into the drag chain, then fix the drag chain to the system
- Use zip-ties to secure cables at both ends of the drag chain
10-b | Pass the whole wire harness to the ERCF connector plate
| • Add the NEMA17 pancake motor cable to the wire harness from the selector, anchor the whole harness to the Block_End part using the

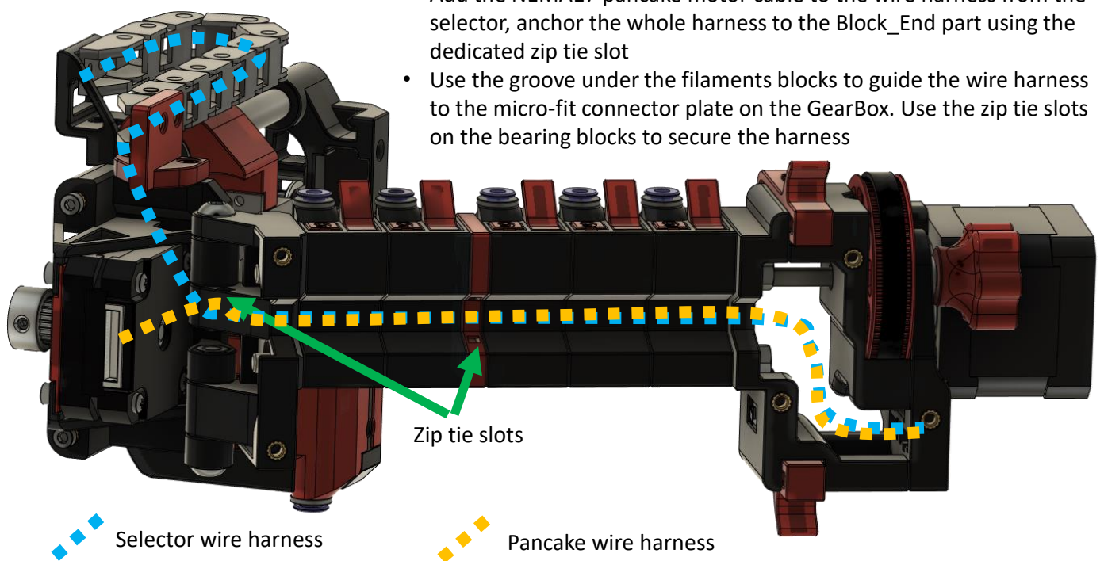
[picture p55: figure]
Zip tie slots; dedicated zip tie slot; Selector wire harness; Pancake wire harness

| • Use the groove under the filaments blocks to guide the wire harness to the micro-fit connector plate on the GearBox. Use the zip tie slots on the bearing blocks to secure the harness
10-c | Install the 2 ERCF feet

Don’t pinch the wire
harness under the 2 feet!

## 11 Install the selector belt

11-b Adjust the 8mm rods

Screws for the
adjustement
- Use the screws on the selector-motor side to finely adjust the 8mm rods position. The goal is to

match the 3 domes pattern on the Idler_Block on the ones of the Gear_Box_Top. You should be able to lock the two latches without any issues when you close the top block.

11-c Install and tension the selector belt

M3x20 SHCS

- Use the belt_tensionner and a M3x20 SHCS screw to tension the 6mm GT2 belt. Ensure nothing is bending due to overthightening
11-a | Install the Gear_Box_Top | 3x M3x8 SHCS

Gear motor
cable groove

# Main assembly of the ERCF is done! Good job!

## 12 (Optionnal) Installation on a Voron V2

12-a Choosing a connector output

- There are two possibilities for you to wire the ERCF to your Voron V2, either using the MicroFit3 connectors leftovers you should have after building the V2 or using JST-SM connectors
- Build your ERCF cable accordingly, using the following guidelines :

12-b Connections in the electronics compartment

- You may have noticed that we didn’t install the servo arm yet! Don’t worry, this will be done in step 13!

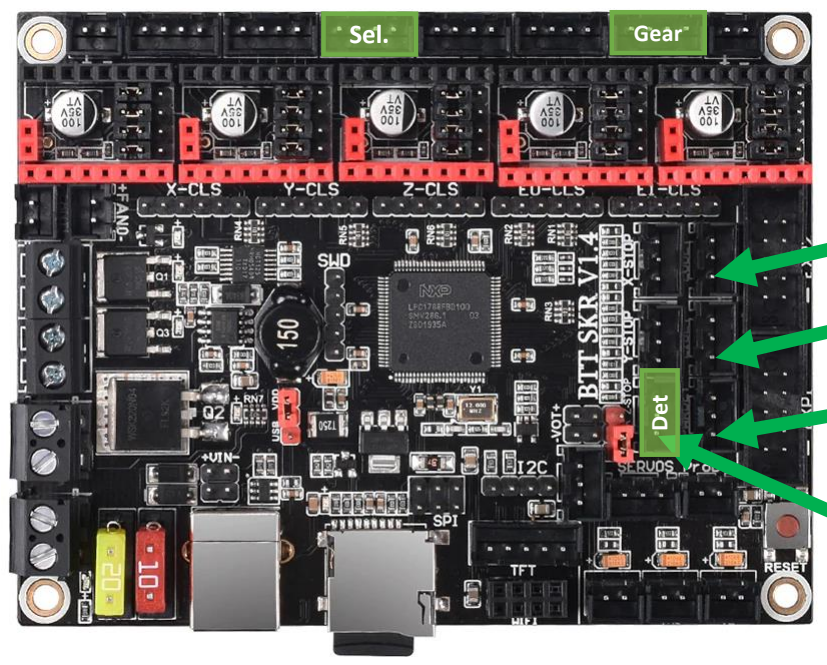
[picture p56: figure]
Sel.; Gear; Det

S for Selector Motor

(the pancake), 4 pins

G for Gear Motor
(the big one), 4pins

Main connector, 5 pins

5V

GND
Servo PWM

Endstop signal

Optical sensor signal

- This is an exemple, you can adapt it to your setup of course. Only mandatory part is to use the 5V/GND from the Rpi power supply (the 5V 5A you should have), servo are power hungry and it won’t behave that well if the current is drawn from the SKR

Endstop signal (pin 1.25)

Optical sensor signal (pin 1.0)

Toolhead filament detector (5V, GND and signal)

Servo PWM (pin 1.26)

MicroFit3 in the back panel JST-SM in skirts

‘XY//AB’ SKR Board

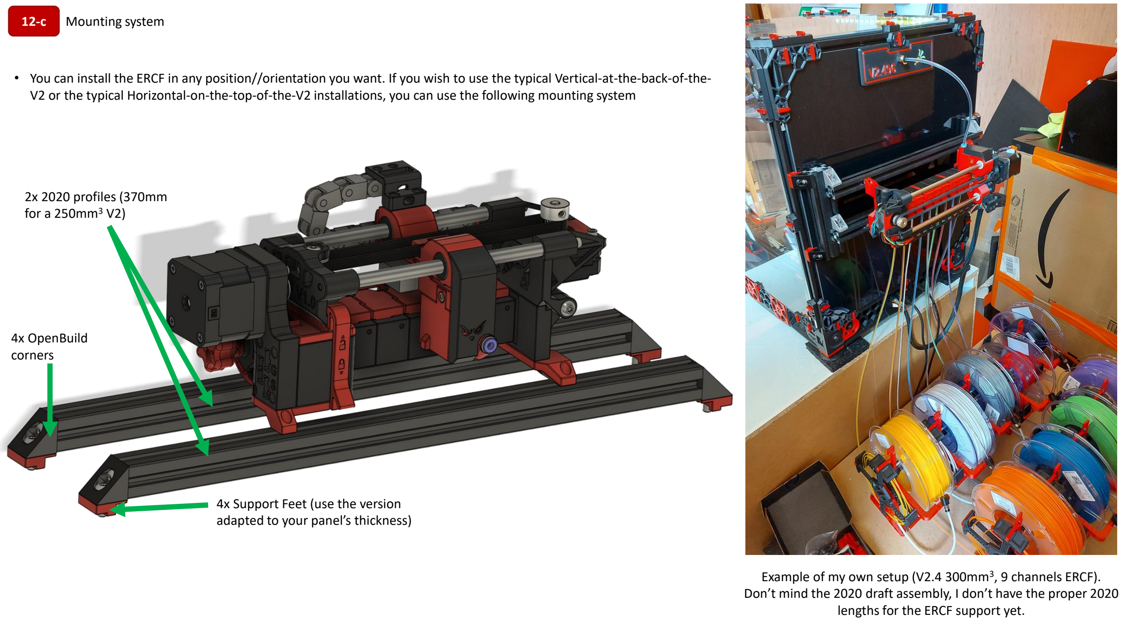
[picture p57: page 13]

12-c Mounting system

- You can install the ERCF in any position//orientation you want. If you wish to use the typical Vertical-at-the-back-of-the-V2 or the typical Horizontal-on-the-top-of-the-V2 installations, you can use the following mounting system

4x OpenBuild
corners

2x 2020 profiles (370mm
for a 250mm³ V2)

4x Support Feet (use the version adapted to your panel’s thickness)

Example of my own setup (V2.4 300mm³
, 9 channels ERCF).
Don’t mind the 2020 draft assembly, I don’t have the proper 2020 lengths for the ERCF support yet.

## 13 First steps with the ERCF

13-a | Install the servo arm
13-c | Check that both motors are ok
13-b | Calibrate the filament detector • Before you plug//unplug the ERCF from your printer, remember to turn off the
printer motors
- Once plugged-in, the first step is to install properly the servo arm
- Use the SERVO_DOWN command (you should hear the servo briefly turning)
- Insert the servo arm into the servo gear, so that the arm matches the « down » position, as shown below
- Use a M2x6//8mm screw to firmly attach the servo arm on the servo gear

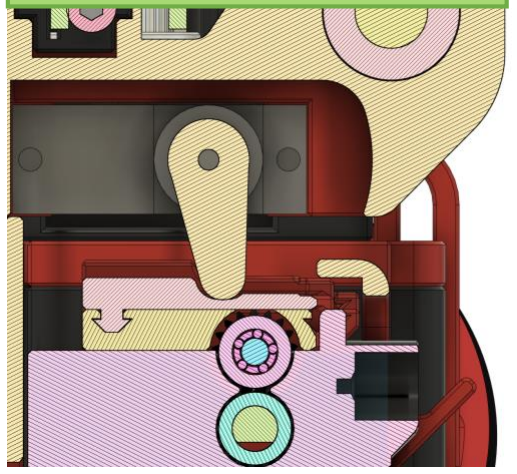
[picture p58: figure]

- Once properly fixed, use the SERVO_UP and SERVO_DOWN macro to check that :
- SERVO_UP puts the servo in a position where the arm won’t hit anything when the selector is moving
- SERVO_DOWN puts the servo arm in the proper filament locking position (same as shown above)
- If necessary, you can adjust both angles in the ercf_macros.cfg header (resp. variable_servo_up_angle and variable_servo_down_angle values). Play with the SERVO_TEST VALUE=XX (XX being the angle) to test different values before editing the config file and rebooting the firmware.
Typical UP position | Typical DOWN position
- First, use STEPPER_BUZZ STEPPER=<config_name> to check that the motors are properly connected
- Check that they’re both rotating in the proper direction : going positive on the Gear Motor should make the filament go out of the ERCF (selector side) and going positive on the Selector motor should make the selector go away from the selector endstop (i.e. the mechanical switch). To do that just use MANUAL_STEPPER STEPPER=config_name SET_POSITION=0 followed by
MANUAL_STEPPER STEPPER=config_name MOVE=<pos>, with pos being a small number (less than 10). If needed, change motor rotation direction in the cfg.
- Check both motors calibration (e-steps and steps/mm) and tune it properly
- Open fully the ERCF (open the two side latch and rotate the top axis) to have a proper access to the selector bottom screws
- The 2 Optical sensor calibration screws are used to move the optical sensor up and down inside the detector cart
- Start with the sensor at the max high position (optical sensor as close as possible to the 8mm rods), you don’t need to force at all. Also remember to keep the optical sensor « horizontal » (i.e. do one turn per screw at a time). Optical sensor should be « ON » (i.e. red light)
- Make sure no filament is inserted in the selector cart
- Make the optical sensor go down until the red light turns OFF (be very precise there, you want to be at the edge of the ‘ON’ signal
- Put a filament in/out of the selector cart to check that:
- The light is OFF when there is no filament
- The light turns bright red (ON) as soon as you push the filament through
- You can close the ERCF

Optical sensor
calibration screws

13-c Home the ERCF

- Make sure all previous steps are properly done and that the ERCF is properly closed
- Load filaments in the ERCF : put the filament in its channel, make it go through the filament block and even more, then push what’s out of the filament block back in with your finger. Filament should be now flush at the filament block exit
- Use the HOME_ERCF macro : this will first eject a filament (if there is one detected, that should not be the case here), then home the selector and then try to preload the 1st channel
- Preloading means that the selector will reach the 1st channel (i.e. the one next to the selector endstop), engage the bondtech gears with the servo and push the filament until it is detected by the optical sensor in the ERCF. Once done, filament will be pushed slightly out of the selector cart, and then put back in its filament block
- Note that the parking position of the filament, when done by the ERCF, is deeper into the filament block : the filament tip won’t be flush on the filament block exit, this is intentionnal

Check the console to see if everything went fine (it is quite verbal ;) )

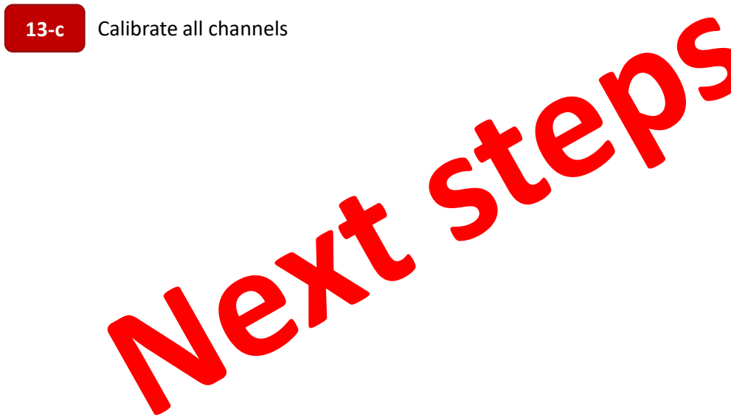
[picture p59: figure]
Calibrate all channels

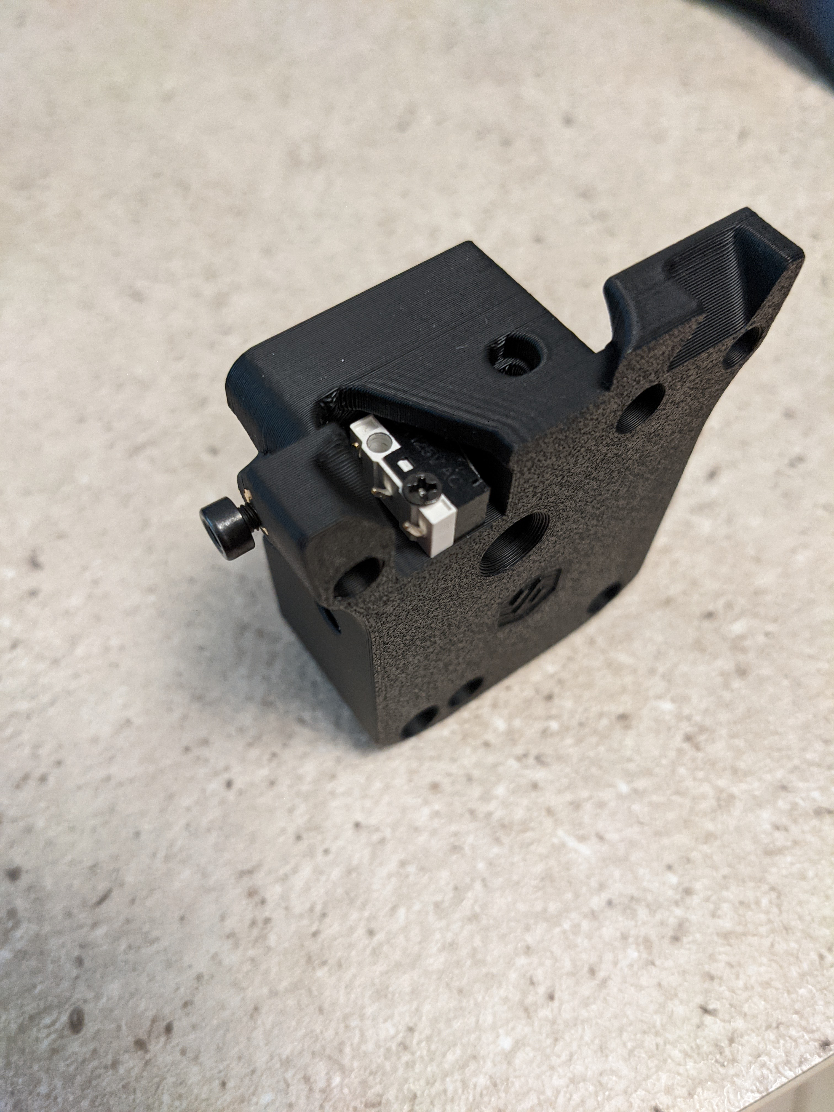
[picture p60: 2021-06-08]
usermods/AB_Toolhead_Sensor/PoorMans_NEW_Smartwatch/Images/AssemblyExample.jpg

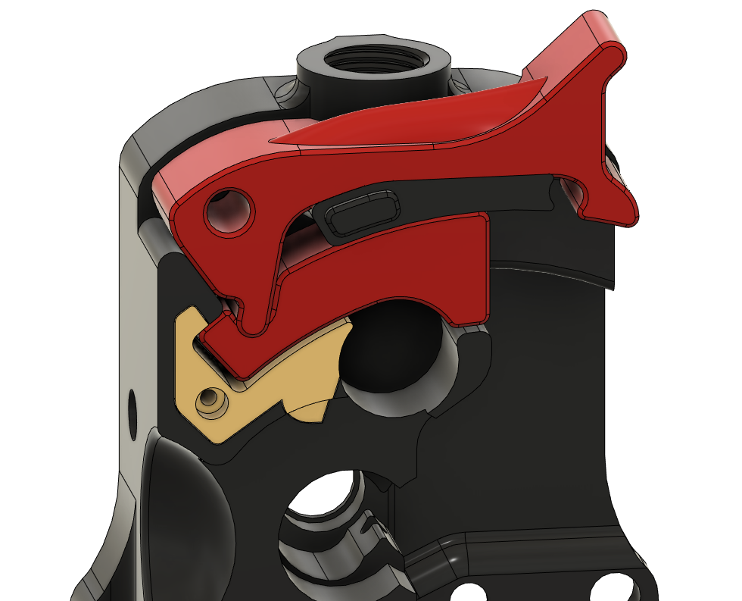
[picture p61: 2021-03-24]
usermods/AB_Toolhead_Sensor/Images/AssembledClockwork.PNG

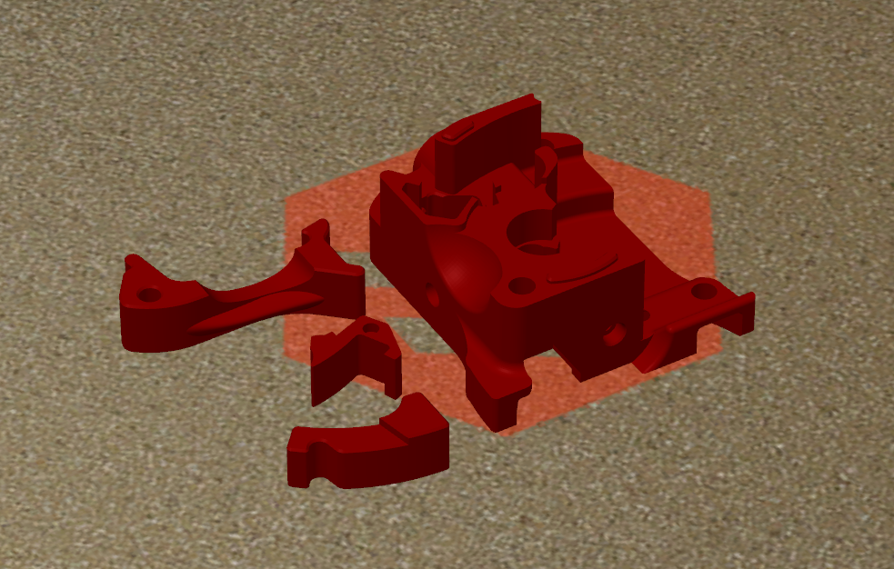
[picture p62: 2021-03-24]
usermods/AB_Toolhead_Sensor/Images/PrintOrientation.PNG

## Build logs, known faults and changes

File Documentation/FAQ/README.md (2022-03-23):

# Enraged Rabbit Project F.A.Q.

Here is the FAQ for the Enraged Rabbit Project.
Check the .md files for each sub part of the project.

### General
**Q: In what material should this be printed with?**  
**A:** The whole design assumes it's printed in ABS. However, several users printed their unit in PLA or PETG, without apparent issues.

**Q: What materials can be printed with the Enraged Rabbit?**  
**A:** So far, PLA, PETG, ABS and TPU were all tested with success. For TPU, both 95A and 30D (~80A) were tested and could be loaded//unloaded using the Enraged Rabbit Carrot Feeder. While the 95A TPU was also working well with the Carrot Patch spool holder + buffer combo, the 30D TPU is way too soft to make filament "loops". If you plan to use such ultra-soft TPU, make sure the concerned Carrot Patch is located in a "clean" area (to avoid your TPU buffer length to be caught on something) or use another buffer//spool holder.

**Q: Can I use this system on another printer than a VORON V2?**  
**A:** Yep, as long as your printer is running Klipper you should be good to go. Make sure the toolhead you are using have a filament sensor below the extruder gear or at the idler itself, like on some MK3 Bear Extruder versions. VORON AfterBurner, Galileo and LGX on AfterBurner are officialy supported, but plenty other toolheads have been modified to fit such a sensor, look in the usermods folder of this repo.

**Q: Can I use a dedicated control board?**  
**A:** Of course, Klipper allows you to use as many MCUs as you want. In the end you'll need to control 2 stepper motors, 1 5V servo, 1 mechanical switch, 1 IR sensor and 1 filament detector. You can find a dedicated PCB, made by @Tircown, here : https://github.com/Tircown/ERCF-easy-brd.

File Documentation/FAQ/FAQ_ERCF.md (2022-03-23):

# Enraged Rabbit Carrot Feeder (ERCF) F.A.Q.

Here is the FAQ for the Enraged Rabbit Carrot Feeder.

**Q: My encoder (TCRT5000) is always on/red, what is going on ?**  
**A:** Remove the TCRT5000 from the encoder cart and check that:
	- It is off when there is nothing in front of the sensor
	- It turns on / red when you bring something reflective in front of it, like
	a metallic tool

If the sensor is always on / red even if there is nothing in front of it, it is 
probably dead (either DOA or you miss-plugged the 5V into the signal for example).

Make sur you did print the encoder_cage in a black filament, to avoid IR reflections.

Don't forget to use the M3x16 SHCS bottom screw of the encoder cart to adjust the sensor height relative to the BMG gears.
You can also use a M3x8 SHCS on the hole below the bearing "spring" to increase the spring tension on the ilder, in case you need to.

**Q: When performing the test grip, using higher Top Hat Lockers makes the servo arm go back after the "_ERCF_SERVO_DOWN" move, lowering the grip on the filament.**  
**A:** Increase a bit the servo_down angle so it pushes further.

**Q: While everything is working fine on TX commands out of a print, during a print the servo will engage and then directly disengage before the unload move.**  
**A:** This is a Klipper issue with servos and timing. If this happens to you, adjust a bit the variable_extra_servo_dwell_down value in the ercf_software.cfg, this will add some ms of dwell for this sequence and fix your issue. Don't forget to reload the firmware for it to work. Try increments of 2, but remember that maybe you'll need 2, 5 or even. Note that this issue cannot be predicted, as it is related to the hardware (mcu, servos) you are using.

**Q: My printer issued a "Move out of range" error after the resume following and ERCF_PAUSE.**  
**A:** Make sure you are using the proper PAUSE and RESUME macros from the Enraged Rabbit GitHub repository (in the client_macros.cfg) and that no other similar macros are in your Klipper config files. What is happening here is that other PAUSE and RESUME macros are being used, and the printer restarts the print in the relative positioning mode, resulting in moves that are out of the print area.

**Q: Sometimes the gear motor is making a very loud and high pitch noise.**  
**A:** This means the motor is skipping. Make sure there are no mechanical constraints on the 5mm D-Cut shaft. For instance, make sure that the tension on the 188GT belt is not too high (there is no need for high tension on the ERCF) and that the two 5mm threaded rods are not overtighten, as this will cause the whole ERCF to bend.
Also make sure that the configuration is matching your motor properties (current, accel, speed, stealthchop threshold etc.)

**Q: What are the 2020 extrusion length for the V1/V2 support.**  
**A:** They are the same as the horizontal profiles on your printer. For instance on a V2 300 those are 420 mm long.

**Q: The toolhead hall effect sensor is not working**  
**A:** First, make sure you are using the proper hall effect sensor (i.e. AH3364, nothing else).
Second, beware that low-strength magnets will not work properly. Try to get a N51 or N52 grade magnet.
Third, you need proper M3 DIN125 ferromagnetic washers. This means you need Steel (galvanized or zinc-plated for example), not Stainless Steel. Also make sure the washer is free of any bur, otherwise it can be stuck in its groove.

If you still have issues, make sure that the hall effect sensor is properly installed in its slots and firmly secured (using the dedicated screw) and remember to test both magnet polarities.our motor properties (current, accel, speed, stealthchop threshold etc.)

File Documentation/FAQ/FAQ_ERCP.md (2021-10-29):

# Enraged Rabbit Carrot Patch (ERCP) F.A.Q.

Here is the FAQ for the Enraged Rabbit Carrot Patch.

### General
**Q: How does this work?**  
**A:** The spool holding part is a direct copy of the nominal spool holder on Vorons, i.e. an arm with a 4mm PTFE tube on which the spool rests and turns around. The buffer part of the Carrot Patch, which is inspired from several similar open-source designs, consists of a big wheel located in a filament "cage". Filament from the spool enters the filament cage, makes a few turns around the wheel and then exit the cage through a PTFE tube. When the extruder pull filament during a print, the filament will encircle the buffer wheel, which will simply turn to go along with the extruder pulling. When there is a retract // unload, the filament will be pushed back in the filament cage, making big loops (as much as the cage allows, so roughly 15 cm diameter), storing the filament buffer length in the cage. More filament turns around the wheel implies a longer buffer length. Use 4 turns to form a buffer of around 120 cm. 

**Q: Why not use a spool rewinder instead of a buffer?**  
**A:** Usual rewinders are using either a spring or a counterweight of some sort (nuts, bearing, spool itself...). The result is that it will rewind a certain number of spool turn, not a defined filament length (an almost empty spool will have a very small rewinding capabiliy). Also VORON V1s and V2s are big printers and the reverse bowden is usually quite long (around 80cm), meaning that typical rewinding solutions are not enough anyway. On the other hand, a buffer like the one on the Carrot Patch can handle very long filament buffer length.

**Q: The buffer wheel recess on the buffer cross has a smaller diamater than the buffer wheel itself, is this normal?**  
**A:** Yes. Goal of this recess is just to reduce the total contact surface between the wheel and the buffer cross "wall", while conserving a direct contact with the edge of the wheel.

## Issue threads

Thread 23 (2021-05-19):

[Request] Please include *.f3d Fusion 360 CAD models if possible (as well as the STEP files)

NameOfTheDragon, 2021-05-19:
I know you've included STEP files for all the CAD models, which is great. It allows easy import into Fusion 360 for viewing the model.

However, the problem with STEP files is that they do not capture the design history, so you end up with an object with no access to the sketches, features and operations that went into creating it. Don't get me wrong, that's better than a poke in the eye, but it does make modding much more difficult than it strictly needs to be. It is so much easier if you can go back and tweak a sketch or edit a feature, or insert new operations in the timeline to modify existing features. All this is lost when exporting as a STEP file.

I don't know that you were working in Fusion 360 of course, but it's an educated guess that you likely were.

So my request is - if possible - and if you are willing - please include the *.f3d Fusion 360 files as well as the step files.

EtteGit, 2021-05-22:
Hello Tim,

While I understand your request, I clearly don't feel confortable enough sharing the parts history. Right know, in the rush of releasing it, many parts have been "hotfixed" on the go. While I wouldn't mind sharing the history on a clean part, we're not there yet.

If this need is to tweak tolerances for a print in PETG, I strongly advise, still, to use ABS. That way you'll end up with a similar setup as others, making possible troubleshooting much less painful.

Now if you want to do a "small" mod for a part or two, I can send to, by PM, the f3d for the concerned parts only.

Best regards,

Ette

syscod3, 2021-08-31:
If that is the case, why the project is not clearly marked as in alpha stage for the benefit of anyone?

EtteGit, 2021-08-31:
@syscod3 Well, a "dirty" cad history doesn't mean a dirty//bad CAD file...

Also, already on the front page since day first :
"You'll find more informations about each of those components into their respective folders. Note that this is a work in progress !!"

Mynasru, 2021-10-04:
@EtteGit Maybe an in-between solution would be to create a "dirty" branch in git so people can enjoy both your proper and hot fixed work 😃

Closed 2022-06-17.

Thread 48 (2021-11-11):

Calibration not possible

Durahl, 2021-11-11:
Greetings,

I've concluded most of my ERCF build but I'm now struggling with the **ERCF_CALIBRATE** process on page 116 of the [Build Manual](https://github.com/EtteGit/EnragedRabbitProject/raw/main/Documentation/ERCF_Manual.pdf).

**Maybe some details about the Printer** - It is a 350 sized Voron 2.4 with the ERCF attached to its side and with the OD=4mm / ID=3mm PTFE Tube still going through a ( side feed ) Exhaust Port Filter - The total length of that PTFE Tube was measured at 1110mm:
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
Mounting the ERCF to either the back or top of the Voron to shorten the Tube is not an option because of the limited space in my closet leaving only a Slot Cut at the top as a last resort option. The Afterburner Toolhead uses the [Poor man's SmartWatch MOD](https://github.com/EtteGit/EnragedRabbitProject/tree/main/usermods/AB_Toolhead_Sensor/PoorMans_NEW_Smartwatch).

The issue I'm having are best described in the following 3 pictures:
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
There appears to be an issue with the Unloading stdev being high despite the moves being relatively consistent?
The Gap between the "Wall" of the IR-Sensor and the BMG Idler ( mentioned on page 107 ) is probably less than 1mm after filing down the Sensor supporting plastic.

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
When subtracting 50mm from the 1100mm measured PFTE Tube [the Filament stops like 10cm before reaching the Toolhead, keeps creeping forwards and then times out](https://youtu.be/AiQnylkwYxE) in **Octoprint**.

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
After significantly increasing the PTFE Tubes reported length in `ercf_software.cfg` to reach the Toolhead Sensor before the Timeout happens it now stops with the Filament remaining in contact with the Sensor without the supposed retraction happening and thus also no other Tools other than T0 being calibrated.

What is causing the problem?

EtteGit, 2021-11-11:
Hi! Thanks for all the details, makes it easy to help :)

First, encoder :
- your values aren't perfect, but still in the somehow usable range
- to improve that, make sure the gears are clean (the part seen by the ir sensor as well as the filament 'teeth')
- if it's still the same, try another bmg idler. Some users have reported some 'off specs sized' idler causing issues like yours

Second, 'unable to save variable' error message :
- make sure the path in the [save_variables] section in the ercf_software.cfg links to the ercf_vars.cfg. it seems not to be the case for you right now

Third, the timeout issue. This is purely an octoprint issue, not an ercf one. Octoprint is expecting the mcu to report regularly some heartbeat signal, even during lengthy
 commands. Apart from switching away from Octoprint (I personally strongly encourage you to at least try mainsail and/or fluidd), look here https://community.octoprint.org/t/timeout-configuration/13130/2.

Also note that Octoprint will likely override stuff like the T0, T1 etc commands and the Pause and Resume ones.... so you'll have to make sure that the macros from the ercf repo are not skipped.

Durahl, 2021-11-11:
Thanks for the help!

The following has happened so far:

- I've relocated the `ercf_vars.cfg` to the proper folder to be used in Octoprint - Fluidd / Mainsail, which the Manual relies on, apparently have a different Folder structure.
- I've replaced the Sensor BMG that came with the ERCF Set with an entirely different one from a complete BMG Extruder Set I had intended for use in another Extruder. I also shaved down a little more of the IR Sensor supporting plastic to get it closer to said BMG - They now make eeeeeever so slight contact without binding resulting in fairly different numbers:
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
The Load/Unload numbers are now more in line with each at the cost of the stdev now having gotten worse for Load but improved for Unload - 3.6 Röntgen, I guess?
- Those changes so far allowed me to do a full `ERCF_Calibration` - Changing the Single Toolhead to a 6xShared one in Octoprint allowed me to test the Tn Command successfully to load but unloading would again take so long it would cause a Timeout and with me not knowing which commands to add in the Link you provided I decided to move on...
- So, I decided to give **Fluidd** a shot using a 2nd SD Card.
Lots of problems... Most of which I could fix by adapting some logic from the process of building the Voron itself like Fluidd now complaining about there be missing `rotation_distance`, `gear_ratio` values, and the `microsteps` ones being under the wrong section ( Drivers instead of Steppers ) - Is this a Fluidd quirk it being so picky or is this perhaps a new Klipper Version issue that came with the Fluiddpi Installation on the new SD Card? Octoprint sure wasn't complaining about this.

Yeaaa... As I'm writing this, I noticed that only your **non** ERCF Easy-Brd `ercf_hardware.cfg` is providing those missing/proper settings. Probably something to look into? 😉
- Aanyway... I'm now stuck with this error Message:
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
Already having seeked for help in the Fluidd Discord it appears that I'm required to recompile the MCU Firmwares?
The BTT Octopus V1.1 has already received a Firmware onto its SC Card from the klipper/out folder that came with Fluiddpi I installed today - Shouldn't that provide the most recent version? Same for the ERCF Easy-Brd one that wasn't even 2 days old! If not, where am I supposed to get current firmes from? 🤔

Durahl, 2021-11-12:
Some progress and some not...

Puh... I figured out how to deal with the above mentioned Firmware Problem - Hella Task to get a new Firmware onto that BTT Octopus V1.1 Board using a special Bootloader - Updating the ERCF Easy-Brd was less of an issue once you know that you know you can identify it using `ls -l /dev/serial/by-id/*` and just use `sudo /usr/local/bin/bossac -i -d -p /dev/ttyX -e -w -v -R --offset=0x2000 out/klipper.bin` instead of the half a kilometer long `/dev/somethingsomethingetc... variant.`

Fluidd though is still not happy and is as undescriptive as ever:
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
All I could figure out is the error disappearing once I **exclude** `[include ./ercf_software.cfg]` from the `printer.cfg` but obviously this isn't an option with that file being _kinda_ important? Taking a peek into printer.cfg for `ercf` revealed 359 results - meh?! 😑

I obviously had some edits to mine already made ( like changing the Encoder Pin to `encoder_pin: ^ercf:PA6` instead of `encoder_pin: ^P1.0` ) but even using a "clean" `ercf_software.cfg` from your GitHub had the error appear.

phil65, 2021-11-12:
that means that you missed copying the ercf.py file to the klippy/extras folder.

Durahl, 2021-11-12:
Argh... The darn changing Folder Structure between Octoprint and Fluidd... I need to stop working on unfamiliar stuff until early/tired into the mornings 😑

Thanks for the help!

Durahl, 2021-11-13:
I have returned 😅

Just for everyone's sanity - Is there a way to communicate with other ERCF Builders that have already built and successfully used the system to get the load off Etty providing support? 😉

Anyway... I've now _"successfully"_ printed my first ERCF Part...
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
...but that took a lot of pampering from my side and some sacrifices along the way...

1. Like predicted in the Manual on Page 124 - My **Purge Line** is part of my `PRINT_START` G-Code Macro which is now obviously broken as there'll be no Filament at the time of the Purge:
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
Being the simpleton that I am I tried to just split the code in two like how it is shown in the Manual Example with `BRUSH_TOOL_PURGE LENGTH=80.0 PARKMOVE=0` with the Purge being a new one separate from the original to have it executed after the Filament would have been loaded using `PRINT_START2` in the Slicer:
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
but Fluidd disagreed with that:
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
Can you maybe also provide your entire `PRINT_START` G-Code Macro ( with the `BRUSH_TOOL_PURGE LENGTH=80.0` portion ) as a reference?

2. As can be seen on the next picture:
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
My Purge Tower has a significant buildup in the area the Toolhead comes to a stop - I assume I'm loading the Filament too far during the Loading sequence? I'm pretty sure I can also hear some skips in the toolhead from the overpressure.

Using **F360** - I Frankensteined a Mosquito HF / Poor man's SmartWatch Toolhead 3D Model together ( PTFE Tube doesn't enter that deep into the Extruder housing ) to get the proper measurements described on Page 126/127:
**ercf_software.cfg**
`variable_end_of_bowden_to_sensor: 44.0`
`variable_sensor_to_nozzle: 60.0`
**SuperSlicer**
`Cooling tube position: 38`
`Cooling tube length: 20`
`Filament Parking position: 58`
`Extra loading distance: -57.8`
I assume I'd ideally want for the Extruder to purge thin air during the first moves and gradually start ramping up as actual filament enters the nozzle but like described above there's already heaps of extra filament on the purge block once the loading has finished - My Mosquito is kinda leaky so it may already be an issue while unloading? 🤔 IDK...

3. Babysitting...
I noticed **unused** Filament T1 ( or any other unused T2-5 ) _also_ getting ever so slightly unloaded even further withing their Filament Blocks during the unloading of the currently used Filament T0 causing it to leave the area where the BMG Gear could reach it once it's being requested - Any suggestions for _that_ issue? Creating a Kink in the PTFE Tube ( or using thinner ID ones ) that feed into the Filament Blocks to increase friction in hopes for that friction overpowering unwanted unloading of any Filament not engaged by the `ERCF_SERVO_DOWN` pressing onto its Filament Top?

EtteGit, 2021-11-13:
For the blobs of plastic after a load : you need to tune the sensor_to_nozzle variable. Reduce it to reduce the blobs, until they are no more :)

phil65, 2021-11-14:
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

Your PRINT_START2 macro is missing the "gcode:" line.

EtteGit, 2021-11-28:
Can I close this issue or is there something left you need help with?

Durahl, 2021-12-02:
I'm good, thanks =)

Closed 2021-12-02.

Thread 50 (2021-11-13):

ERCF calibrate failing

lerou114, 2021-11-13:
I have successful run all my calibrations and I am on the step to calibrate the ercf when I run the calibration I have set the bowden length in config 5 cm shorter than length when I run the ERCF_CALIBRATE command when I get to the part where the filament feeds to the filament to the extruder I have klipper shutting down every time.

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

I reran the encoder calibration and I get exact 200 mm measurements multiple times during encoder calbration step. I'm at a lose as to what I am doing incorrectly. I have also replaced the usb cable because I had found some users where having issues with poor quality usb cables.  What should I be looking for?

EtteGit, 2021-11-13:
Make sure the klipper version on your MCUs matches the one on your rpi

lerou114, 2021-11-13:
I just checked  there was a version mismatch so I have flashed everything to the newest version of klipper, but I am still getting the error.  Currently this is my version:
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

EtteGit, 2021-11-13:
Ok, thanks.  Can you provide the klippy.log when this error occurs please?

lerou114, 2021-11-13:
So I cleared my log file and recreated the condition I happened to find this in the log at line 1820:
Heater extruder not heating at expected rate
Transition to shutdown state: Heater extruder not heating at expected rate
See the 'verify_heater' section in docs/Config_Reference.md
for the parameters that control this check.

[klippy.log](https://github.com/EtteGit/EnragedRabbitProject/files/7532518/klippy.log)

EtteGit, 2021-11-13:
Indeed, but the timer took close issue appears right at the call of the ERCF_HOME_EXTRUDER. I guess the issue comes from this function (located in the ercf.py). I don't know yet why it's happening to you

lerou114, 2021-11-22:
I found the issue was due to my own error in the extruder configuration my rotation distance was not set properly. I had upgraded all my firmware to a newer version prior to installing the ERCF. I did not do any prints without the ercf to verify my standalone configuration was properly working with the newest firmware. Once I revised the rotation distance this fixed the mcu time out issue.

Closed 2021-11-22.

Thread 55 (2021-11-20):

Screws for switchwire mounts exist... NO NUTS for said screws can be found

tnap1979, 2021-11-20:
i can locate the threaded printable screws for the ercf to mount to the frame, but cannot locate the nuts to lock them in place

EtteGit, 2021-11-20:
The threads are on the parts on the '2020' and '3030' folders (3030 being for the switchwire). There are no nuts.

tnap1979, 2021-11-20:
Oh jeez... wow.. I'm blind.. haha..
Ok, well in that case.. can close this..
Just built myself a 4port feeder and patch setup..
Dude... your design and setup of this device... blows my mind... are you an engineer of sorts?? Amazing work..  thanks for this project

EtteGit, 2021-11-20:
:) I'm glad you like it!

tnap1979, 2021-11-20:
Forgot to ask.. as I'm unsure where to look...
Is there an afterburner motor mount plate that has a heatset insert for the toolhead board that supports the rabbit v3 toolhead board??
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

EtteGit, 2021-11-20:
You'll find what you want here I think https://github.com/VoronDesign/Voron-Hardware/tree/master/Afterburner_Toolhead_PCB/STLs/Clockwork

tnap1979, 2021-11-20:
I did.. thanks soooo much again..
😀

Closed 2021-11-20.

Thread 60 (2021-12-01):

Reducing change time

JiMcNulty, 2021-12-01:
The ERCF is amazing, great work.
If you did not consider it, I may have an idea to speed up change:

 - Add a filament cutting mechanism
- Cut the current filament when the calculated material needed is in the length of the bowden (some custom code)
- Push new filament
- The new one will push the old one
- Purge the new one

This way the machine will keep printing while swapping, with a minimum time to optimize to spend on purging

One downside is that if the swap need to happen every n < length of bowden you either will have to purge and waste filament or restrict the minimum amount of swap

Another downside is in flexibles, you will need to push the new one while the extruder pull the old one

EtteGit, 2021-12-01:
Thanks =)

The cut and use the filament until the extruder is something I've thought of quite some time ago, but the amount of work slicer // klipper wise to make it happen is THE issue I don't want to deal with right now.

Now if you, or anyone else, feels the courage to code that, I'll be happy to put a cuter in the ERCF 1.1 ^^

the-cobbler, 2021-12-01:
Give me a month or so and i'll be available :)
I have a current side quest of trying a POC of a bed probe using an accelerometer + gyroscope board

EtteGit, 2022-01-26:
Hi =) Just checking if I can close this issue or you still want it open.

Cheers

JiMcNulty, 2022-01-26:
Smash that close button

JiMcNulty, 2022-01-26:
Smash that close button

Closed 2022-01-26.

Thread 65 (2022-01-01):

Mistakes in the BOM

vladimir-poleh, 2022-01-01:
Hi,

I have found that BOM contains incorrect quantity for some fasteners.
It should be 28 instead of 26 for the M3 threaded inserts and 22 instead of 20 for the  M3x8 SHCS.

mattddonnelly, 2022-01-26:
This should all be on the base nominal ERCF:
7x gear box front
4x gear box back
1x gear box motor arm
2x filament block end
3x selector cart
2x drag chain anchor
3x encoder
4x selector motor support
2x drag chain anchor bottom

EtteGit, 2022-02-22:
I've updated the BOM, sorry for the long delay.
Cheers,
Ette

Closed 2022-02-22.

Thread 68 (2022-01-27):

ERCF Overloaded?

Teila, 2022-01-27:
Greetings,

I have been getting an excessive amount of 'Timer too close - Shutting Down' issues when I am doing toolhead swaps during a print and when I am just manually cycling the tools for testing.

This is one of the latest logs after a crash.

[klippy (11).log](https://github.com/EtteGit/EnragedRabbitProject/files/7946596/klippy.11.log)
.

phil65, 2022-01-27:
Also experienced that issue once, in my case it was a loose cable connection of the infrared sensor. Perhaps worth checking.

Anathema-Device, 2022-01-27:
Hi Teila, I have seen this when trying to restart a test and also a divide by zero at the end of the calibration of feeder 0 when one would expect it to start feeder 1.  I updated to the latest ercf_software.cfg and ercf.py and that seems to have reduced the errors but ercf_calibrate does bizzare things now.

It does the feeder 0 calibrate OK without the divide by 0 issue but then does some sort of partial calibrate on feeder 0 but the messages indicate the subsequent feeders, weird.

Teila, 2022-01-27:
> Also experienced that issue once, in my case it was a loose cable connection of the infrared sensor. Perhaps worth checking.

I have not seen any issue with my sensor disconnecting randomly. Perhaps a way to log the count rate vs the turn signals sent to the feeder on a load/unload for debugging is needed?

Teila, 2022-01-27:
> Hi Teila, I have seen this when trying to restart a test and also a divide by zero at the end of the calibration of feeder 0 when one would expect it to start feeder 1. I updated to the latest ercf_software.cfg and ercf.py and that seems to have reduced the errors but ercf_calibrate does bizzare things now.
>
> It does the feeder 0 calibrate OK without the divide by 0 issue but then does some sort of partial calibrate on feeder 0 but the messages indicate the subsequent feeders, weird.

I also have had divide by zero on some calibration runs but whenever that happens I notice that is directly related to the filament not moving. I have had the servo not lock down when running the calibrate, the filament not get grabbed, filament get stuck temporarily in the extruder. However, those times it produces the divide by zero. My current issue occurs when I see the filament moving and the sensor (to my eye) is functioning (blinking) per normal.

EtteGit, 2022-03-17:
Hi,
I'm closing this thread since the other one is more active and concerns the same kind of issue (which should be fixed in the upcoming commits)

Closed 2022-03-17.

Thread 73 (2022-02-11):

Newest Version of klipper breaking extras module

Beraval, 2022-02-11:
After Updating to the newest version of klipper I am presented with this error.

Internal error on command:"ERCF_HOME"
Internal Error on WebRequest: gcode/script
Traceback (most recent call last):
  File "/home/pi/klipper/klippy/webhooks.py", line 245, in _process_request
    func(web_request)
  File "/home/pi/klipper/klippy/webhooks.py", line 415, in _handle_script
    self.gcode.run_script(web_request.get_str('script'))
  File "/home/pi/klipper/klippy/gcode.py", line 216, in run_script
    self._process_commands(script.split('\n'), need_ack=False)
  File "/home/pi/klipper/klippy/gcode.py", line 198, in _process_commands
    handler(gcmd)
  File "/home/pi/klipper/klippy/gcode.py", line 135, in <lambda>
    func = lambda params: origfunc(self._get_extended_params(params))
  File "/home/pi/klipper/klippy/extras/gcode_macro.py", line 186, in cmd
    self.template.run_gcode_from_command(kwparams)
  File "/home/pi/klipper/klippy/extras/gcode_macro.py", line 68, in run_gcode_from_command
    self.gcode.run_script_from_command(self.render(context))
  File "/home/pi/klipper/klippy/gcode.py", line 213, in run_script_from_command
    self._process_commands(script.split('\n'), need_ack=False)
  File "/home/pi/klipper/klippy/gcode.py", line 198, in _process_commands
    handler(gcmd)
  File "/home/pi/klipper/klippy/gcode.py", line 135, in <lambda>
    func = lambda params: origfunc(self._get_extended_params(params))
  File "/home/pi/klipper/klippy/extras/gcode_macro.py", line 186, in cmd
    self.template.run_gcode_from_command(kwparams)
  File "/home/pi/klipper/klippy/extras/gcode_macro.py", line 68, in run_gcode_from_command
    self.gcode.run_script_from_command(self.render(context))
  File "/home/pi/klipper/klippy/gcode.py", line 213, in run_script_from_command
    self._process_commands(script.split('\n'), need_ack=False)
  File "/home/pi/klipper/klippy/gcode.py", line 198, in _process_commands
    handler(gcmd)
  File "/home/pi/klipper/klippy/gcode.py", line 135, in <lambda>
    func = lambda params: origfunc(self._get_extended_params(params))
  File "/home/pi/klipper/klippy/extras/ercf.py", line 394, in cmd_ERCF_SET_STEPS
    self.gear_stepper.rail.steppers[0].set_step_dist(new_step_dist)
AttributeError: MCU_stepper instance has no attribute 'set_step_dist'
Dumping stepper 'manual_stepper selector_stepper' (ercf) 2 queue_step:
queue_step 0: t=984515532 p=393 i=59994 c=-1187 a=0
queue_step 1: t=1007956721 p=3 i=0 c=0 a=0

phil65, 2022-02-11:
https://github.com/EtteGit/EnragedRabbitProject/pull/74

Teila, 2022-02-13:
Meaning that the ERCF modules still use the deprecated Set_Step_Dist. =[

I also am now getting an error with the new klipper update
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

Teila, 2022-02-13:
Attached Logs for those that would like it.
[moonraker.log](https://github.com/EtteGit/EnragedRabbitProject/files/8054812/moonraker.log)
[klippy (12).log](https://github.com/EtteGit/EnragedRabbitProject/files/8054813/klippy.12.log)

Anathema-Device, 2022-02-13:
https://github.com/EtteGit/EnragedRabbitProject/pull/74/commits/ff60a56bc3e6e2bf0fbb2385c55872d678c90078

EtteGit, 2022-02-22:
>

The fix has already been merged on the ercf side, please update your ercf.py =)

EtteGit, 2022-02-22:
I'll keep this issue open for a few weeks, just for people to see easily what the fix is.

EtteGit, 2022-03-23:
Time to close this =)

Closed 2022-03-23.

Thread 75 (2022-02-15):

MCU 'ercf' shutdown: Timer too close

FHOGPHIL, 2022-02-15:
ok - got this a couple of times now
MCU 'ercf' shutdown: Timer too close
This often indicates the host computer is overloaded. Check
for other processes consuming excessive CPU time, high swap
usage, disk errors, overheating, unstable voltage, or
similar system problems on the host computer.
Once the underlying issue is corrected, use the
"FIRMWARE_RESTART" command to reset the firmware, reload the
config, and restart the host software.
Printer is shutdown

cpiercedev, 2022-02-15:
Are you using easybrd?

FHOGPHIL, 2022-02-16:
>

yes

FHOGPHIL, 2022-02-16:
Seems similar to #68

FHOGPHIL, 2022-02-16:
at least 4 times now and each time on an unload to switch tools mid print

amv101, 2022-02-17:
I am also getting this error on my Delta printer with ERCF. I didnt have this error until I installed the ERCF system on my Klipper powered Delta just this week. I will run the test print again and try to attach the klippy log and gcode.

Specs-
Delta printer, Bondtech Extruder, E3D V6 nozzle, AC powered bed via SSR
Octopus v1.1 mainboard, 24VDC, Steppers A,B,C = TMC2209 UART, NEMA 17
Raspberry Pi 4B 4GB, connected USB
Klipper
Octoprint
ERCF v1.1, Steppers = TCM2209 UART, NEMA 17 (No EasyBRD, wired direct to Octopus)

FHOGPHIL, 2022-02-22:
Thought it might be a camera issue so pulled camera.  didnt help,  On the unload command, the filament got out of the extruder and when the high speed unload started, it dies

Unload move done, requested = 857.0, measured = 1.3
Correction unload move done, requested = 857.0, measured = 1.3
Too much slippage detected during the unload, please check the ERCF, calling ERCF_PAUSE...
MCU 'ercf' shutdown: Timer too close
This often indicates the host computer is overloaded. Check
for other processes consuming excessive CPU time, high swap
usage, disk errors, overheating, unstable voltage, or
similar system problems on the host computer.
Once the underlying issue is corrected, use the
"FIRMWARE_RESTART" command to reset the firmware, reload the
config, and restart the host software.
Printer is shutdown

FHOGPHIL, 2022-02-22:
RPi 4B 2GB/SSD EZBRD and SSD on USB3.0

TravisWilder, 2022-02-22:
I had a similar issue and it was caused by bad soldering spots of the EZBRD

EtteGit, 2022-02-22:
Hi. Just to let you know I'm looking into it. Unfortunately this is a rather vague issue, as this klipper error can be caused by a plethora of different things.

MuddyPuddles4325, 2022-02-22:
I found I could easily reproduce this using the servo in succession. For example if you modify the servo down function to go down, up, then down again with only 200ms between calls it happens every single print. If I make the gap 400ms the problem goes away.

FHOGPHIL, 2022-03-02:
So I found a solution.
every time the command "{% set ercf_params = printer.save_variables.variables %}" comes up I added a line after it that reads "G4 P500".  (Obviously there are no quotation marks.)  This has stopped the error from coming up.

amv101, 2022-03-04:
Had a chance to work on my new Delta with the ERCF 1.1 and attach the klippy log with the error.

I get the "Timer too close" error consistently if I finish a print, restart firmware, then restart the same print in Octoprint. When the filament is being ejected before the start of a new print, the error occurs right when the filament reaches the reverse bowden tube.

[klippy.log](https://github.com/EtteGit/EnragedRabbitProject/files/8187258/klippy.log)

EtteGit, 2022-03-17:
After tinkering yesterday, I found that, for whatever reason, recent Klipper updates made the call of ERCF_UNLOAD right after another command crash the MCU (timer too close).

There is no apparant reason for that to occurs, since calling the commands next to each other by hand won't cause any issue, so it's definitely an issue with how klipper is dealing with its command stack // timing.
That being said, adding a 200ms dwell right at the beginning of the ERCF_UNLOAD command fixed it.
It'll be pushed soon (I need to clean the files still).

EtteGit, 2022-03-23:
The fix is live since a few days. Let me know if the issue still pop back

tonylee1918, 2022-03-25:
I am getting the same issue. I increased the dwell to 0.5s but this is still happening. Details
-Voron v2+easy brd+lgx+dragon HF+klipper expander
-klipper 0.10.0-244
-Issue also happens only on unload
[klippy.log](https://github.com/EtteGit/EnragedRabbitProject/files/8347029/klippy.log)
d

gurusonwheels, 2022-03-26:
still here also
voron 2.4
skr 1.4 turbo dual boards .
easy brd
dragon HF

tonylee1918, 2022-03-28:
Quick update to further nail down issue - this happens to me only if the ERCF goes into "PAUSE"
If all is well, no crashes.
Also I can rule out the presence of the klipper expander board as I have disabled it for a little while now and it still crashes

EtteGit, 2022-04-08:
I've found one source of MCU Timer too close, namely when calling _ERCF_SERVO_UP and _ERCF_SERVO_DOWN one after another from a python module command. I'll use this simple exemple to open a Klipper issue.

In the mean time I've pushed a fix for that yesterday

RealHabix, 2022-04-16:
Still getting it even after last commit (self.toolhead.wait_moves()) - only on unloading.

rwijnhov, 2022-04-24:
I am having the same issue while trying _ECRF_CAlIBRATE it seems to happen after de ECRF_PAUSE get's called.

MCU 'ercf' shutdown: Timer too close
09:45:45
MCU 'ercf' shutdown: Timer too close
This often indicates the host computer is overloaded. Check
for other processes consuming excessive CPU time, high swap
usage, disk errors, overheating, unstable voltage, or
similar system problems on the host computer.
Once the underlying issue is corrected, use the
"FIRMWARE_RESTART" command to reset the firmware, reload the
config, and restart the host software.
Printer is shutdown
09:45:45
Too much slippage detected during the unload, requested = 1183.1, measured = 0.0 - calling _ERCF_PAUSE...
09:45:45
Correction unload move done, requested = 1183.1, measured = 0.0
09:45:45
Unload move done, requested = 1183.1, measured = 0.0

cmroche, 2022-04-28:
I'm able to reproduce this error with ERCF_UNLOAD, and started to investigate. There might be a work around until the issue is clearer, see the conversation here: https://klipper.discourse.group/t/manual-stepper-move-causing-timer-too-close-shutdown/2725

cmroche, 2022-04-28:
I am able to reproduce this problem during print, and very consistently calling `ERCF_UNLOAD` at any time. After some investigation I'm inclined to think the problem is hardware dependant.

In my case I am using an EZBRD (Seeduino), with a 0.9 degree stepper (it's what I had on hand). I had it configured for 16 microsteps, 400 per revolution, with 200 mm/sec speed and 2000 accel. In experimenting with this I found the speed and accel didn't make any difference, bandwidth and MCU load we're both around 30-40% so the seeduino wasn't overloaded. However dropping the microsteps to 8, or changing steps per revolution to 200 fixed the timer too close. Even if the MCU isn't overloaded, the seeduino is not able to handle scheduling the steps reliably if too fast.

cmroche, 2022-04-29:
I'm seeing this problem too, sometimes mid print and fairly reliably when calling `ERCF_UNLOAD`.

I've been investigating for the last couple of days, and noticed that the "timer too close" only happens for some combinations of microstepping and move lengths on the gear_stepper.

For example, this break for me (and all values of MOVE larger than this)

```
MANUAL_STEPPER STEPPER=gear_stepper ENABLE=1
MANUAL_STEPPER STEPPER=gear_stepper SET_POSITION=0
MANUAL_STEPPER STEPPER=gear_stepper MOVE=1200 SPEED=400 ACCEL=2000
```

But this will work (and all values of MOVE smaller than this)

```
MANUAL_STEPPER STEPPER=gear_stepper ENABLE=1
MANUAL_STEPPER STEPPER=gear_stepper SET_POSITION=0
MANUAL_STEPPER STEPPER=gear_stepper MOVE=1000 SPEED=400 ACCEL=2000
```

As a quick workaround, I set my microstepping to **8** and no longer have the error. With interpolation enabled on the TMC2209 there is little change in noise level fortunately.

I suspect the cause of the error now to be numerical imprecision in the step generation. But, it might also be possible that the seeduino is unable to construct and schedule the steps fast enough. Load analysis only shows about 35-40% MCU load, but there may be other factors.

cmroche, 2022-04-29:
It dawned on me, the issue might be latency in solving the steps for the given hardware configuration. More microsteps and a long path means more solving to do. I hacked in a 1 second delay to the start of the step schedule and this resolved the problem, ruling out numerical inaccuracy and scheduling problems.

You won't see particularly high loads on the pi given the timeframes we're talking about here, but it looks like this could explain it.

cmroche, 2022-04-30:
I'm working on a proper fix in Klipper, should have something in a few days time: https://klipper.discourse.group/t/long-manual-stepper-moves-cause-timer-too-close/2740/3

RealHabix, 2022-05-02:
>

@cmroche I changed the microstepping to 8 as well, but still got the error.

Does the commit (splitting long moves) fix the issue?

cmroche, 2022-05-02:
@RealHabix If your timer too close happens on the long LOAD/UNLOAD move then it's possible the commit will fix your issue.

fastlightning, 2022-05-26:
Any general solution for this problem?

cmroche, 2022-05-26:
@fastlightning @EtteGit The simplest workaround for this problem would be to avoid singular long moves with MANUAL_STEPPER and instead break them up into smaller sequences of moves so that the motion planner doesn't stall the queue for too long. This implies ERCF_LOAD and ERCF_UNLOAD mainly, breaking the moves in half would probably fix this problem for the vast majority of users based on my testing.

The PR submitted to Klipper needs more work, while it gives a short term fix and probably you won't experience other problems while using it, there are some corner cases where it will not schedule moves correctly if you try to use SYNC=0, the subsequent moves will not start until the MANUAL_STEPPER move is complete.

EtteGit, 2022-06-17:
The PR from @cmroche was just merged. Let me know how that went for you guys

gunan, 2022-07-17:
I just merged all those changes, but I am still seeing this issue. Here are my logs: https://gist.github.com/gunan/f4cce4e7cb23577da37f670fe48ee576

gunan, 2022-07-17:
Maybe #115 as this is happening during a load move? or load correction?

gunan, 2022-07-19:
I tried reverting #113 to see if the issue gets better, but there are no improvements.
I will try reverting another commit.

One thing I will see if it is related though is, I think before every crash, I see that "Unable to reach the toolhead sensor" message is printed. So, maybe the issue is around [701d38a62d82401237b910eb9194e5e10c37e446](https://github.com/EtteGit/EnragedRabbitProject/commit/701d38a62d82401237b910eb9194e5e10c37e446). Trying reverting that now.

gunan, 2022-07-19:
Not that commit either, will keep looking.

gunan, 2022-07-20:
I was able to root cause my problem as the `m400` calls added py #102 when I remove those, My timer too close issues go away. Other problems arise, but at least I can pause, debug and resume my prints.

cmroche, 2022-08-06:
> I was able to root cause my problem as the `m400` calls added py #102 when I remove those, My timer too close issues go away. Other problems arise, but at least I can pause, debug and resume my prints.

The `M400` is not likely the root cause I'm afraid, all it's doing is adding a delay which causes your RPI's timing to push it over the scheduling threshold by draining the current step queue.

In **ercf_software.py** there is now a variable `variable_num_moves`, start by increasing this to 2 to break up the long moves into multiple subsequent moves, this reduces the step planner delay causing the error.

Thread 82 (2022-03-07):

ERCF_LOAD_FILAMENT_IN_EXTRUDER detect slow?

Teila, 2022-03-07:
Greetings!
Is there any way to add some buffer time to the detection of load into the nozzle? I find it causing a ercf_pause just before the filament detection sometimes.

Anathema-Device, 2022-03-07:
I have no solution but I see this too where an ercf_pause is invoked for some reason immediately followed by a filament loaded message.  My guess is that having the filament sensor on the hotend connected to my old 8-bit board is introducing some feedback lag as the load stepping continues on for a second or so AFTER the ercf_pause is issued.

Imnotkelby, 2022-03-29:
I am having the same problem and have tried adding pauses of lengths up to 2 seconds in between various parts of the ERCF_LOAD_FILAMENT_IN_EXTRUDER macro with no success, but maybe I missed something.

cmroche, 2022-05-07:
@EtteGit The same issue is happening with unload, and a fix (and explanation of the timing problem) is in PR #102 . I made the same fix for _ERCF_LOAD_FILAMENT_IN_EXTRUDER in that change too.

Closed 2022-06-17.

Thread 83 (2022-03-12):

Servo not engaging sometimes

amv101, 2022-03-12:
I have been using the ERFC for a few weeks now, and have gotten most of the things worked out. I have an issue with the servo (MG90S) not engaging sometimes. It is wired directly into my Octopus v1.1 board 5V pin. It happens during feeding and unloading. I have tried all servo angles and top hat lockers, and have tried multiple cables with different lengths. Sometimes it just doesnt make the full swing for contact. The servo arm doesnt pass the bump. It will also do it randomly when homing ERCF or testing the grip. The only thing I havent changed was the servo.

Any ideas?

Benoitone, 2022-03-12:
Hello.
Have you read ERCF FAQ?

amv101, 2022-03-12:
> Hello. Have you read ERCF FAQ?

Looks like it has been updated since I have last checked. I see there might be a timing issue. I will check that after this current print is done. Thanks!

EtteGit, 2022-03-14:
> > Hello. Have you read ERCF FAQ?
>
> Looks like it has been updated since I have last checked. I see there might be a timing issue. I will check that after this current print is done. Thanks!

Does the solution in the FAQ fixed your issue?

amv101, 2022-03-15:
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

I did a 6hr print without any issues. I had to turn the print off, and the printer is down for some maintenance. As soon as I get it back up I will test it some more this week.

I edited this line

```
    SET_SERVO SERVO=ercf_servo ANGLE={printer["gcode_macro ERCF_VAR"].servo_down_angle}
    G4 P200
```

Changed G4 P200 -> G4P205

EtteGit, 2022-03-23:
Everything is solved? Can I close this?

michaelbeljaars, 2022-05-31:
I have a similar problem. With top hats other then #1 the servo does not make the full swing. Changing angles in the configuration does not change that, nor does the proposed solution above of adjusting the timing. It seems the servo does not have enough power to fully press down the the top hat. I have found that top hat #1 does not give me enough pressure on most filaments, but switch to higher hats lead to even less pressure because of the issue with the servo.

When I manually position the servo arm to its full extension, I get the desired grip on the filament.
I am using a MG90S with an ERCF Easy BRD v1.1

Anathema-Device, 2022-05-31:
@michaelbeljaars I had a similar issue and I found that making sure that the top was smooth helped.  Adding a tiny bit of silicon grease or printing the lockers in resin made a big difference.  Also I found that it does not seem to take a huge amount of pressure to get a good grip but the arm has to be fully engaged so that it is in the correct place.

michaelbeljaars, 2022-05-31:
Thanks for your advice @Anathema-Device, I have tried much of what you suggest: smoothing the top hats (sanding, greasing) but that doesn't seem to change the fact that the servo arm can't pass the hump and subsequently relaxes back (and thus not applying pressure).

Anathema-Device, 2022-05-31:
@michaelbeljaars I think if it is catching in the dip in the top of the locker then the locker may be too high?  I also touched the top of each block and the bottom of the top hat with a file to make sure they were all smooth, flat and mated well.  If you lightly touch it the top hat should press down and engage easily but release when you remove your finger.  Everything has to be moving easily.  It is frustrating to get it all working.

michaelbeljaars, 2022-05-31:
No it's not catching in the top dip, it's just not able to push all the way to the lock position and hence it slides back, releasing pressure on the top hat. I've indeed noticed that filing the top hats makes a difference, which makes me question whether even the #1 top hat could be too high for my ercf.

Anathema-Device, 2022-05-31:
Make sure that the top and and the block below both have smooth, flat surfaces so that they mate cleanly and move smoothly.  You could also remove the top hat and make sure that the servo goes from the minimum position next to the servo body (servo_up) to full down position (servo_down) with no load as a start.  The servo down position will likely need to be a smidge further in order to work well.

dominikacri, 2022-06-01:
Had the same problem at the beginning. The servo pushed it perfectly to the lock position and then it was sliding a little bit back after that. The grip was not good. IIt was to weak with 1-3 and with 4 and aboth it was unable to reach the lock final position.

But I did many things wrong like tried to push the servo to 180 degrees. Tested the strength of the servo against my fingers and other bad things. So maybe I destroyed the servo with that :-)

I also ordered the mechanical parts as a set with the servo and maybe the MG90S was a fake. Not easy to know today.

So I reprinted the filament blocks, the lockers and the servo arm and this time the ERCF savox adapter with a better quality and ordered a savox servo which is also supported.

The MG90S has around 1.8kg/cm while the Savox SH0255-MG has around 3.1 kg/cm (depending which side you read more or less :-D)

I changed both together so I cannot say if the better print quality or the savox did the trick but after that the grip was very good.

I also ordered a L7806CV voltage regulator to replace the 5V that is used in the Easy BRD for powering the servo.
Both servos are capable of running with at least 6V with increased holding torque.

2.1kg/cm at 6V for MG90S  3.9kg/cm for the savox but that was not needed in my case. Only a minimal enhancement but dropping from 24 To 6V produces less heat than dropping from 24 to 5 so 2 good things I thought :-D
But I never used it.

But you can test it also with a step down. I saw that newer chinese boards uses also step downs instead of voltage regulators in their Easy BRD boards.

michaelbeljaars, 2022-06-01:
Here are two videos of the servo engaging on of the top hats. As you can seen in both videos it slides a bit back, although in one less than the other.

https://user-images.githubusercontent.com/28304614/171352892-e65e5fe2-8d1c-4012-8098-bc4a62a6360e.mp4

https://user-images.githubusercontent.com/28304614/171352896-aef513e0-8936-48ac-b9c8-e3805bf69395.mp4

I also discovered that some bontech gears were not perfectly aligned with the filament path in the blocks, so I fixed that, but it didn't seem to make much of a difference.

Without any top hat in front of it, the servo basically makes the full swing that it can make with the arm attached, meaning that it almost touches the selector in the down position.

https://user-images.githubusercontent.com/28304614/171353663-55899a61-a0a1-492b-b5a7-e122c27ce2c5.mp4

michaelbeljaars, 2022-06-07:
I just replaced my MG90S for a Savox SH0255-MG, but that made no difference. The servo is still unable to push the top hats fully to the lock position and then slides back.

michaelbeljaars, 2022-06-08:
I have adjusted the hats by creating a more pronounced slot at where the servo arm should rest in the lock position using a circular file. This seems to have solved the problem with the servo arm not getting to the lock position and also results in enough pressure on the filament.

EtteGit, 2022-06-17:
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
EtteGit, 2022-06-17:
> I have adjusted the hats by creating a more pronounced slot at where the servo arm should rest in the lock position using a circular file. This seems to have solved the problem with the servo arm not getting to the lock position and also results in enough pressure on the filament.

Just to mention that, quite some time ago, top hats lockers had such "locking slots" on them. Turned out the bump required to make such a slot was too much of an effort for the servo to overcome for many people, hence this design choice was abandoned.

amv101, 2022-08-01:
> Hi! Your down angle is too "high", i.e. it goes too far. You want the down angle to set the servo arm in a "vertical" position, kind of like where the servo arm ends up after slipping in your videos. This is at this position that the grip will be the best. Also from this position it shouldn't slip anymore

@EtteGit  I am still having some issues with the servo. Sometimes there is an issue as described above, and sometimes the servo doesnt make the full sweep at all. As for the slippage, it seems the servo is disengaged after the servo arm move which causes the servo to slowly move out of position due to vibrations. Is there a way to keep the servo powered why it is engaged? I have built many projects with servos and usually the servo stays powered after a move to make sure the position doesnt change.

amv101, 2022-08-07:
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

@michaelbeljaars Any luck finding out why the servo moves out of position, like a twitch, sometimes after the servo movement? I have 3 ERCF units about 5 months old, and they have always done this behavior. It is not consistent though. Sometimes I can get through a full print without any errors. Sometimes the error plaques me all day.

michaelbeljaars, 2022-08-28:
@amv101 No, not yet. I've had a few weeks of summer holidays (I work at a vocational school). What I've done last is file a little dip in the top hats where the servo arm can hook behind. It is not consistent though and as @EtteGit mentioned, sometimes the locking force is too great for the servo to get to the unlock position.

It seems that for my setup already the #1 top hats are too high for the servo to push them fully into position. I am not sure yet what I will be trying next.

dominikacri, 2022-10-11:
Re: [EtteGit/EnragedRabbitProject] Servo not engaging sometimes (Issue #83)

Had the same problem at the beginning. The servo pushed it perfectly to the lock position and then it was sliding a little bit back after that. The grip was not good. IIt was to weak with 1-3 and with 4 and aboth it was unable to reach the lock final position.
 
But I did many things wrong like tried to push the servo to 180 degrees. Tested the strength of the servo against my fingers and other bad things. So maybe I destroyed the servo with that :-)
 
I also ordered the mechanical parts as a set with the servo and maybe the MG90S was a fake. Not easy to know today.

So I reprinted the filament blocks, the lockers and the servo arm and this time the ERCF savox adapter with a better quality and ordered a savox servo which is also supported.

The MG90S has around 1.8kg/cm while the Savox SH0255-MG has around 3.1 kg/cm (depending which side you read more or less :-D)

I changed both together so I cannot say if the better print quality or the savox did the trick but after that the grip was very good.
 

I also ordered a L7806CV voltage regulator to replace the 5V that is used in the Easy BRD for powering the servo.
Both servos are capable of running with at least 6V with increased holding torque.

2.1kg/cm at 6V for MG90S  3.9kg/cm for the savox but that was not needed in my case. Only a minimal enhancement but dropping from 24 To 6V produces less heat than dropping from 24 to 5 so 2 good things I thought :-D
But I never used it.

But you can test it also with a step down. I saw that newer chinese boards uses also step downs instead of voltage regulators in their Easy BRD boards.

Make sure that the top and and the block below both have smooth, flat surfaces so that they mate cleanly and move smoothly. You could also remove the top hat and make sure that the servo goes from the minimum position next to the servo body (servo_up) to full down position (servo_down) with no load as a start. The servo down position will likely need to be a smidge further in order to work well.
—
Reply to this email directly, view it on GitHub, or unsubscribe.
You are receiving this because you are subscribed to this thread.Message ID: ***@***.***>

--
Mit freundlichen Grüssen
Dominik Acri

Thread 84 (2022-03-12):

Pause commend causing "Move out of range:" issue

amv101, 2022-03-12:
I am running ercf on a custom Delta printer. When a clog is detected, or there is no filament in the cart, I will get a "Move out of range" error when the printer goes into the pause state. I have tried reducing my delta radius by half, to see if there was an issue with the probe offset, but I still get the same error.

Any ideas what the issue might be?

Error from the Octoprint terminal when sending "pause" right after homing / moving down

```
Recv: // Klipper state: Ready
[...]
Send: G28 // homes all axis
Recv: ok
Send: G91 // set absolute move
Recv: ok
Send: G0 Z-50 F1000 // move down 50mm
Recv: ok
Send: G90 // set relative move
Recv: ok
Send: G91
Recv: ok
Send: G0 Z-100 F1000
Recv: ok
Send: G90
Recv: ok
[...]
Send: pause
Recv: // action:paused
Printer signalled that it paused, switching state...
Recv: !! Move out of range: -145.000 145.000 245.085 [-1.000]
Recv: !! Move out of range: -145.000 145.000 245.085 [-1.000]
Recv: ok
```

printer.cfg

```
# This file contains common pin mappings for the BigTreeTech Octopus.
# To use this config, the firmware should be compiled for the
# STM32F446 with a "32KiB bootloader" and a "12MHz crystal" clock reference.

# See docs/Config_Reference.md for a description of parameters.

[include ./ercf_hardware.cfg] # ERCF settings
[include ./ercf_software.cfg] # ERCF settings

# Driver0
[stepper_a] # StepperOnline 17HS19-2004S1, 1.8 degree, 2A
step_pin: PF13
dir_pin: !PF12
enable_pin: !PF14
microsteps: 16
rotation_distance: 40
endstop_pin: PG6
#position_endstop: 385
homing_speed: 80
homing_retract_dist: 5.0
second_homing_speed: 3
#arm_length: 400

# Driver1
[stepper_b] # StepperOnline 17HS19-2004S1, 1.8 degree, 2A
step_pin: PG0
dir_pin: !PG1
enable_pin: !PF15
microsteps: 16
rotation_distance: 40
endstop_pin: PG9

# Driver2
[stepper_c] # StepperOnline 17HS19-2004S1, 1.8 degree, 2A
step_pin: PF11
dir_pin: !PG3
enable_pin: !PG5
microsteps: 16
rotation_distance: 40
endstop_pin: PG10

# Driver3
# The Octopus only has 4 heater outputs which leaves an extra stepper
# This can be used for a second Z stepper, dual_carriage, extruder co-stepper,
# or other accesory such as an MMU
#[stepper_]
#step_pin: PG4
#dir_pin: PC1
#enable_pin: PA0
#endstop_pin: PG11
#...

# Driver4
[extruder] # Bondtech LGX, 1A, 400 steps/mm
step_pin: PF9
dir_pin: !PF10
enable_pin: !PG2
microsteps: 16
rotation_distance: 7.84 # Bondtech LGX 400 steps/mm
nozzle_diameter: 0.400
filament_diameter: 1.750
heater_pin: PA2 # HE0
sensor_pin:  PF4 # T0
sensor_type: EPCOS 100K B57560G104F
#control: pid
#pid_Kp: 22.2
#pid_Ki: 1.08
#pid_Kd: 114
min_temp: 0
max_temp: 250
min_extrude_temp: 0 # enables cold extrudes for calibration
max_extrude_only_distance: 200 # ERCF settings
max_extrude_cross_section: 50.0 # ERCF settings
pressure_advance = 0.190 # lower the value for more rounded corners 0.192 default

[probe]
pin: PG12 # ! to invert pressure probe
x_offset: -15.0 # pinda=-15.0
y_offset: 14.0 # pinda =14.0
#z_offset: 0.0
speed: 2.0
samples: 3
sample_retract_dist: 3.0

#[filament_switch_sensor material_0]
#switch_pin: PG12

# Driver5
#[extruder1]
#step_pin: PC13
#dir_pin: PF0
#enable_pin: !PF1
#heater_pin: PA3 # HE1
#sensor_pin: PF5 # T1
#...

#[filament_switch_sensor material_1]
#switch_pin: PG13

# Driver6
#[extruder2]
#step_pin: PE2
#dir_pin: PE3
#enable_pin: !PD4
#heater_pin: PB10 # HE2
#sensor_pin: PF6 # T2
#...

#[filament_switch_sensor material_2]
#switch_pin: PG14

# Driver7
#[extruder3]
#step_pin: PE6
#dir_pin: PA14
#enable_pin: !PE0
#heater_pin: PB11 # HE3
#sensor_pin: PF7 # T3
#...

#[filament_switch_sensor material_3]
#switch_pin: PG15

[heater_bed]
heater_pin: PA1
sensor_pin: PF3 # TB
sensor_type: ATC Semitec 104GT-2
#control: pid
#pid_Kp: 22.2
#pid_Ki: 1.08
#pid_Kd: 114
min_temp: 0
max_temp: 130

[fan]
pin: PA8

[heater_fan fan1]
pin: PE5
heater: extruder
heater_temp: 40.0

#[heater_fan fan2]
#pin: PD12

#[heater_fan fan3]
#pin: PD13

#[heater_fan fan4]
#pin: PD14

#[controller_fan fan5]
#pin: PD15

[display]
lcd_type: uc1701
cs_pin: EXP1_3
a0_pin: EXP1_4
rst_pin: EXP1_5
contrast: 63
encoder_pins: ^EXP2_5, ^EXP2_3
click_pin: ^!EXP1_2
## Some micro-controller boards may require an spi bus to be specified:
#spi_bus: spi
## Alternatively, some micro-controller boards may work with software spi:
spi_software_miso_pin: EXP2_1
spi_software_mosi_pin: EXP2_6
spi_software_sclk_pin: EXP2_2

[output_pin beeper]
pin: EXP1_1

[neopixel fysetc_mini12864]
pin: EXP1_6
chain_count: 3
color_order: RGB
initial_RED: 0.4
initial_GREEN: 0.4
initial_BLUE: 0.4

[mcu] # Rasp Pi USB
serial: /dev/serial/by-id/usb-Klipper_stm32f446xx_350034000750534E4E313120-if00
# CAN bus is also available on this board

[mcu rpi] # Rasp Pi local mcu for ADXL345 Accel.
serial: /tmp/klipper_host_mcu

[adxl345] # Acelerometer
cs_pin: rpi:None

[resonance_tester]
accel_chip: adxl345
probe_points:
    0, 0, 340  # toolhead x y z location during test

[input_shaper]
#shaper_freq_x: 59.4
#shaper_type_x: mzv
#shaper_freq_y: 59.0
#shaper_type_y: mzv

[printer]
kinematics: delta
max_velocity: 300 # default 300
max_accel: 3000 # default 3000
max_z_velocity: 200 # default 150
square_corner_velocity: 3.0 # default 5
#delta_radius: 201.027
print_radius: 150
minimum_z_position: -10.0 # used for initial calibration

[delta_calibrate]
speed: 200
radius: 140
horizontal_move_z: 2

[bed_mesh]
speed: 200
horizontal_move_z: 2
mesh_radius: 130
mesh_origin: 0, 0
round_probe_count: 9
mesh_pps: 4
algorithm: bicubic
bicubic_tension: 0.2
move_check_distance: 5
split_delta_z: .025
#fade_start: 0
#fade_end: 10
#fade_target: 0

[endstop_phase]

[pause_resume] # ERCF settings
recover_velocity: 300.0

########################################
# TMC2209 configuration
########################################

[tmc2209 stepper_a]
uart_pin: PC4
##diag_pin: PG6
run_current: 1.4
hold_current: 0.800
stealthchop_threshold: 0

[tmc2209 stepper_b]
uart_pin: PD11
##diag_pin: PG9
run_current: 1.4
hold_current: 0.800
stealthchop_threshold: 0

[tmc2209 stepper_c]
uart_pin: PC6
##diag_pin: PG10
run_current: 1.4
hold_current: 0.800
stealthchop_threshold: 0

#[tmc2209 stepper_]
#uart_pin: PC7
##diag_pin: PG11
#run_current: 0.650
#stealthchop_threshold: 999999

[tmc2209 extruder]
uart_pin: PF2
run_current: 0.60 # 0.5-0.7 recommended for Bondtech LGX
hold_current: 0.300
stealthchop_threshold: 0

#[tmc2209 extruder1]
#uart_pin: PE4
#run_current: 0.800
#stealthchop_threshold: 999999

#[tmc2209 extruder2]
#uart_pin: PE1
#run_current: 0.800
#stealthchop_threshold: 999999

#[tmc2209 extruder3]
#uart_pin: PD3
#run_current: 0.800
#stealthchop_threshold: 999999

[board_pins]
aliases:
    # EXP1 header
    EXP1_1=PE8, EXP1_2=PE7,
    EXP1_3=PE9, EXP1_4=PE10,
    EXP1_5=PE12, EXP1_6=PE13,    # Slot in the socket on this side
    EXP1_7=PE14, EXP1_8=PE15,
    EXP1_9=<GND>, EXP1_10=<5V>,

    # EXP2 header
    EXP2_1=PA6, EXP2_2=PA5,
    EXP2_3=PB1, EXP2_4=PA4,
    EXP2_5=PB2, EXP2_6=PA7,      # Slot in the socket on this side
    EXP2_7=PC15, EXP2_8=<RST>,
    EXP2_9=<GND>, EXP2_10=PC5

# See the sample-lcd.cfg file for definitions of common LCD displays.

# A [probe] section can be defined instead with a pin: setting identical
# to the sensor_pin: for a bltouch
#[bltouch]
#sensor_pin: PB7
#control_pin: PB6
#z_offset: 0

#[neopixel my_neopixel]
#pin: PB0

## Custom Menus
[menu __main __test]
type: list
name: Tester
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
FHOGPHIL, 2022-03-12:
Are you using the pause and resume macros specifically for ERCF?

RomRider, 2022-03-13:
It's probably related to being in relative vs absolute positioning somewhere in your macros

amv101, 2022-03-13:
There is definitely something up with that setting. From some searching, it has something to do with the probe offsets and the mesh possibly. My Delta has a print radius of 150mm and a print height about 340mm. I run the delta calibration and mesh at 130mm.

When I use this setting, the issue goes away…

```
[gcode_macro PAUSE]
rename_existing: BASE_PAUSE
gcode:
  {% set x_park = printer.toolhead.axis_minimum.x|float + 55.0 %}
  {% set y_park = printer.toolhead.axis_maximum.y|float - 55.0 %}
```

Now it will park at -95.00 95.00 without any issues.

Maybe I should run the delta calibrate and bed mesh with the same radius as the print radius?

amv101, 2022-03-13:
> Are you using the pause and resume macros specifically for ERCF?

Yes... I run the "pause" command from the Octoprint terminal.

FHOGPHIL, 2022-03-13:
> > Are you using the pause and resume macros specifically for ERCF?
>
> Yes... I run the "pause" command from the Octoprint terminal.

That’s not what I asked. Did you replace the klipper pause ad resume macros with the ones from the ERCF GitHub?

amv101, 2022-03-13:
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

I assume so, but I am pretty new to Klipper. I never added any pause macros to my printer.cfg file, except for the ercf macros. I added the ercf macros and then type "pause" into the terminal via Octoprint.

My cfg file is posted above with the macros I have. Would there be another place to check for conflicting klipper pause macros?

amv101, 2022-03-15:
> The "ercf compatible" pause and resume macros are in the "client_macros.cfg" file on the ercf repo (klipper file folder).
>
> Those are the one you need to use with the ercf (or adapt the ones you have to contain the ercf stuff).

Thanks for the help. I posted my cfg above. Did you see an issue with how I added the ercf macros? Not sure why I am getting the error on my delta. Does it have something to do with my bed mesh radius, delta calib radius, and delta print radius being different?

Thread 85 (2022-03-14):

Ptfe tube from hotend cant enter the cw1

Z3ytrox, 2022-03-14:
The ptfe tube of the hotend cant enter the ercf ab cw1 extruder. Therefor Its pressed against the hole that sometimes lead to failed loads. The filament is sometimes pushed against the ptfe tube instead of inside the ptfe tube. Any fixes for this?

Z3ytrox, 2022-03-14:
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 (Normal AB)
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
(ERCF AB)

claytono, 2022-03-14:
This is called out on page 76 of the manual.  You have to use a shorter PTFE tube.

Z3ytrox, 2022-03-14:
Yeah ive seen that but how do you solve the issue thats caused by this? The filament thats running into the ptfe instead of through it?

Closed 2022-03-17.

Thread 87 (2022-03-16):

ERCP: Buffer_Wheel does not "fit" into Buffer_Cross cavity

fabikroeger, 2022-03-16:
Hi There,

i have been assembling the ERCP. While doing so, i have experienced, that the buffer_wheel does not spin freely as i would like to have it spinning. I spotted a friction between Buffer_Wheel and Buffer_Cross. With a closer look it seems for me that there is a cavity in which the buffer_wheel shoult spin but it is not big enought. As marked on the screenshot.
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

For my understanding the fix would be to have a cylinder, slightly bigger than the buffer_wheel substracted from the buffer_cross.
I did that and it looks good for me for now but i want to ask if i do not understand my right.
The next picture shows a fix, which  would be to have a cylinder, slightly bigger than the buffer_wheel substracted from the buffer_cross.
I did that and it looks good for me.
Pink: old buffer_cross
Grey: new buffer_cross
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

Do we have the slightly smaller cavity for the buffer_wheel by intention or is my fix doing his job?

Greetings

FHOGPHIL, 2022-03-16:
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
All nine of these move fine. Any chance you over tightened the center bolt?

fabikroeger, 2022-03-16:
Ah ok thanks for the fast answear, less surface == less friction. Thx! hm, may be yes.
I am building this here : https://github.com/probably-Erwins-Cat/ERCF-Buffer-Array
I need a buffer on the outside of my filament box.
And maybe i have by its design more friction there.
I will have a check on that tomorrow and come back then.

TravisWilder, 2022-03-16:
> Any chance you over tightened the center bolt?

but also let it to loose as else the filament can make it beside the buffer wheel

fabikroeger, 2022-03-17:
Okay, fixed. Thank you all for the hints and suggestions!!
1. To much infill for my first layer of the buffer wheel. So it has had to much friction. The knife helped there.
2. The centerbolt is now proper tightened.

fabikroeger, 2022-03-18:
-

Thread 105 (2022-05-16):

Usage of ERCF with flex filament

michaelbeljaars, 2022-05-16:
Not so much an issue as a question and challenge I guess. I did some investigating online but was not able to find any relevant information on this topic. I have been trying to use the ERCF with flex filament (specifically Ninjatek's Cheeta). Given the appropriate top hat, the filament indeed loads to the extruder, but then prompts an error:

```
14:19:38
An issue with the ERCF has been detected and the ERCF has been PAUSED
14:19:37
idle_timeout: Timeout set to 72000.00 s
14:19:37
Filament seems blocked between the extruder and the nozzle, calling _ERCF_PAUSE...
```

even though it seems to be properly loaded (I can extrude, and the toolhead sensor is triggered). When ejecting, the filament frequently is not unloaded enough in the extruder and stays stuck between the extruder gears when the ERCF is trying to unload.  Loading ABS and PLA works fine, so I am sure that it is related to the stretch that is inherent in flexible filaments. Anyway, I am curious if others have tried the ERCF with flexible filaments and also if there are steps to take to maybe get it to work.  I know that flexible filaments are difficult to work with loading systems like the ERCF (I also have a Prusa MK3S with MMU2S, which just doesn't allow you to use flexible filaments).

EtteGit, 2022-06-17:
Hi! Very flex filament should be doable with the ERCF. This error you got is just the result of the flex behavior of the filament impacting some ercf security check.

Just redo the calibration for the final_load_check_threshold that is mentionned at the very end of the manual, using this flex filament, and you should be totally fine =)

Closed 2022-06-17.

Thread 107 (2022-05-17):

MCU 'mcu' shutdown: Timer too close when select T1

PatrickYCY, 2022-05-17:
When i select the T1 slot th machine will show MCU 'mcu' shutdown: Timer too close
Please find the attached file for you action

[klippy (1).log](https://github.com/EtteGit/EnragedRabbitProject/files/8710639/klippy.1.log)

Anathema-Device, 2022-05-17:
Have you looked at:
https://github.com/EtteGit/EnragedRabbitProject/issues/75 or
https://github.com/EtteGit/EnragedRabbitProject/issues/68

cmroche, 2022-05-26:
Based on this line in the log, it looks like the timeout happens after starting a long move. It's the last command sent before the timeout I believe:

```
Sent 99 176.661427 176.658867 64: seq: 1e, queue_step oid=9 interval=64009049 count=1 add=0, queue_step oid=9 interval=8821 count=11 add=-617, queue_step oid=9 interval=3462 count=23 add=-75, queue_step oid=9 interval=2028 count=42 add=-18, queue_step oid=9 interval=1366 count=69 add=-6, queue_step oid=9 interval=1009 count=76 add=-3, queue_step oid=9 interval=826 count=73 add=-2, queue_step oid=9 interval=704 count=130 add=-1, queue_step oid=9 interval=599 count=74 add=-1
```

This would indicate that you are hitting issue #75

EtteGit, 2022-06-17:
I'm closing this thanks to the nice @cmroche PR for the long move splitting trick =)

Closed 2022-06-17.

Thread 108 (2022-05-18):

CAD files out of date for encoder cart

ajmirsky, 2022-05-18:
Hi, the encoder cart is great! The adjustable height with the screw made it so much easier to calibrate and improve the accuracy of the encoder. Would it be possible to share the CAD files for the updated design? Thanks!

cullinaire, 2022-12-06:
I would also like to see the CAD file for this, especially for the TCRT Off Center Anchor as the provided STL's M3 hole is a bit too large causing the board to wobble.

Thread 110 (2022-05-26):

ERCP High Friction

Durahl, 2022-05-26:
Greetings!

Been using the ERCF / ERCP for I think like 9 months or so and the StealthBurner / ClockWorkd2 on my Voron 2.4 since it was released to the Public with my own MODs to make the CW2 ERCF compatible.

Two exhaustive printing weeks must have worn down my Beta 0/1 CW2 Toolhead Parts down to the point where - I assume - The Guidler and/or Latch may have gotten bent out of shape just enough for the Gears to not be digging in enough anymore to overcome the always present friction in the ERCP > ERCF > CW2 Filament Path thus resulting in frequent Filament Grindings and failed Prints - With the necessity of printing new parts I decided to give the recent CW2 Beta 7-11 Parts a try which turned out to be even worse but while I was it I went ahead and traced the cause of the friction back to the off tangential Filament Exit Port of the ERCP:
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
Basically... Whenever the Filament was stuck and ground to an Hourglass shape in the Toolhead I checked where it may have been stuck by pushing it back but couldn't feel any resistance but pulling it beyond the point where it became stuck was almost impossible.
Taking the Buffer Zone out of the equation would mostly solve this so the issue must be there ( my wheels are spinning freely and the Spools too have been placed on bearings.
For the time being I've resorted to not be winding the Filament onto the wheel and instead just use two PTFE Tubes with one connected to the ERCP PTFE Entry Block and the other to the ERCF Filament Block causing them to split apart if the Filament is being retracted and butt together when the FIlamen is being Extruded.

I'll probably do a DIY MOD of the ERCP to see if this can be solved by printing a Buffer Cross with the Entrance / Exit ports pointing perpendicular towards the Wheels Inner Diameter and thus not introducing that kink in the Screenshot.

I've also noticed certain Filament having a tendency of liking to get pushed out between the rear and bottom Cross sections thus spilling outside instead of coiling up inside - Maybe a wall connecting/closing those two could help with this? 🤔

Anathema-Device, 2022-05-26:
I have a similar issue and tried simple mods to let me push the PTFE further through with the hope that it would result in less friction but that was not 100% successful either.  What I observe that in the jammin' case it seems that coils have contracted overlapping so that there is much increased drag and it stalls the extrusion.    Would a slight thread on the wheel help to set up the path better?  Maybe that with an adjustment like you describe would make it work more reliably.

Personally though I'm looking at the enclosed vertical columns that some have demo'd as a way to contain the retracted filament and keep it isolated and dry.

Durahl, 2022-06-03:
So, here's my take on the suggested changes...

In the first two pictures the Filament now enters the PTFE Tube without the chance of forming a Kink:
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

The third picture shows the restraining "fence" I was talking about:
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
May have to add a ridge to it if the Filament slides off which is like a sub 5min print...

Not pictured but I've also changed the entry Geometry of the PTFE Slider on the Arm to the shape of a Funnel gradually feeding into the PTFE Tube after noticing the orifice on the stock ones having developed a deep groove from the filament sliding through it potentially being the trigger for the kink later down the PTFE road 😑

Currently testing how it is going 😁

I'll probably have to have a look into the ERCF itself if there's a similar problem with the filament having carved a groove at some location creating another Friction Hotspot 🤔

EtteGit, 2022-06-17:
Nice work on this ! Don't forget to do a PR for this Carrot Patch mod, I want to try those changes =)

jwhite, 2022-08-01:
I too would like a PR.  I'm finding this is my #1 source of failure, and am looking at the geometry in fusion.

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

NameOfTheDragon, 2022-09-21:
Interesting. I have had similar problems with high friction, but I have traced it to a different source: the wheel. On the inside of the cross-arm, there is a circular inset that is a little smaller then the wheel. The rim of the wheel rubs up against the cross arm generating friction, and this will be particularly bad if you printed on textured PEI. This has always seemed like an odd design choice to me, as it tends to undermine the inclusion of a ball bearing on the axle. Tension in the filament at this point increases friction all the was along the rest of the feed path, so the closer to the spool it can be eliminated, the better. My usermod is submitted at PR #155 if you'd like to give it a go. Since we have edited the same part, it might be worth combining these mods at some point, once they have got some testing and feedback from users.

jwhite, 2022-09-22:
Thanks @NameOfTheDragon - I was noticing that I have two points of friction, one where the coils have yet to align, and then later once they have all gotten tight.  I wonder if this might resolve the latter?  It's very strange because sometimes there is almost no friction when manually pulling the filament from the extruder end of the tube and sometimes it won't even budge.  I'm using prints on a textured PEI - so I would be seeing what you might have resolved.  Let me print off one of yours combined with one of mine.

Cheers!

3D-Printing-Nerds, 2022-12-30:
Durahl Can we get a copy of the files for your mod on the clockwork2
I want to build a stealthburner to use with my ERCF but i cant find one with the Hall Sensor built in to it

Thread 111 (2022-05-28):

ECAS vs. PC4-M10 on Carrot_Patch/STLs/Buffer_Cross.stl

Jaans, 2022-05-28:
Hello Ette - more of a question than an issue but thought the response might help others.

Between all the different fittings (ECAS, Pressfit, UM2, PC4-M10, PC4-M6, Straight-through, etc.) I'm trying to understand if there is a particular benefit of using ECAS over say PC4-M10?

I happen to have a number of PC4-M10 fittings on-hand and wondered if I could adapt the step files (my CAD skills permitting) and change the Buffer Cross to use a PC4-M10 fitting instead of ECAS?

Could you share some insight of why ECAS might be better? Also, when is the straight through connecter better (or even why does it exist)?

PS: I'm going down the proverbial "rabbit hole" 🐰 with ERCF (waiting on parts) & ERCP (using Ikea 365+ 10l drybox) and enjoying it very much. Thank you (and all that helped) for creating and sharing something amazing!

Anathema-Device, 2022-05-28:
Having PC4-M10 fittings an no extra ECAS I just tapped an M10 thread into the ECAS hole and screwed it in.  Seems to be holding ...

Jaans, 2022-05-30:
Ooo... never thought of that. No need to mod the CAD designs then. I'll give that a go! Thank you 👍

I see no obvious functional difference between ECAS04 and a PC4 type fitting in that the one doesn't have better "holding" capability than the other. In fact, the PC4 type seems more convenient as it doesn't require a clip because it is spring loaded.

All I can think of is that ECAS04 is cheaper, lighter, smaller - which makes sense for it's use on the Carrot Feeder.

Closed 2022-06-05.

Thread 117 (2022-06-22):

Speed factor more than 120% cause loading fail with MCU 'ercf' shutdown: Timer too close

ksdj55, 2022-06-22:
I've encountered a MCU 'ercf' shutdown: Timer too close while using SuperSlicer2.4, after some investigation this error seem to be repeatable by setting speed factor with M220 S200 (or anything above S120) follow by T0 or ERCF_EJECT command.

Also with ERCF_EJECT there was a message "Too much slippage detected during the unload, requested = 1136.6, measured = 0.7 - calling _ERCF_PAUSE..." right before MCU shutdown. (never has loading failure with speed factor at 100%)

I'm using mainsail v2.2.0, klipper v0.10.0-494-gd3c4ba48 on Voron v2.4R2 350 with FYSETC Easy-BRD (based on RP2040) and BTT Octopus 1.1 with Raspberry Pi Zero 2w running mainsail v2.2.0, klipper v0.10.0-494-gd3c4ba48 on Voron v2.4R2 connect through a USB hub, Not sure if it probably a hardware specific problem anyway.

Procedure are:
- Heat extruder
- Set speed factor to 200 (or anything > 120)
- Change tool (T0/T1/T2)

My proposed temporary solution would be something like:

[gcode_macro _ERCF_CHANGE_TOOL]
description: Perform a tool swap
gcode:
    {% set speed_factor = printer.gcode_move.speed_factor %} ;Save previous speed factor
    M220 S100 ;Clear Speed factor
...........

    M220 S{speed_factor * 100.0} ;Restore Speed factor

Thank you.

EtteGit, 2022-06-23:
The "Too much slippage detected during the unload" is simply the consequence of the Timer too close issue (no unload move is performed, so indeed it measures nothing).

I need to investigate more in depth, but to me it's most likely due to the computing power of the pi Zero 2w combined with long, fast and with high micro-stepping moves :
The pi need to compte a calculation heavy move and when it is sent to the MCU, it's a tiny bit too late (from a schedule POV), which trigger the error.

I'll try to somehow replicate this issue and propose a fix, I'll let you know

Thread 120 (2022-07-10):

Implement slaved extruder using gear motor to improve filament feed performance

baccula, 2022-07-10:
High friction filament paths (particularly when using ERCP) plague many ECRF setups. Klipper offers a feature which allows [additional stepper](https://www.klipper3d.org/Config_Reference.html?h=extr#extruder1) motors to be slaved to the extruder during printing.

Implementing this method using the gear selector motor to provide additional filament pushing force would mitigate filament drag issues, however it could also introduce issues with filament bunching or being stretched if the stepper calibration between the two motors is not 100% accurate. To overcome this, I suggest adding a periodic 'SERVO UP' command to remove tension and allow the filament path to balance. This could be done iteratively and in theory should not have any affect on the print GCode.

As not all users will need or benefit from this type of setup (or be able to achieve the close calibration tolerances necessary), I suggest using a configurable parameter in ecrf_software.cfg to enable or disable this behavior. In addition, a configuration field allowing user-specified intervals between servo cycles may be beneficial (alternatively, it may be better to just call a servo cycle for every 'x' mm3 of extruded filament, if such a thing is possible).

EtteGit, 2022-07-17:
Hi,

As discussed in the discord channel, I think this is totally doable. The only issue this can cause is during a clog. I'm afraid of filament grinding by the ERCF gears before the encoder can sense the clog. But this is something worth a try! Have you tried something alredy?

RickDnamps, 2022-11-14:
Any news for this Enhancement ??? I would be a nice add-on !

RickDnamps, 2022-11-15:
I tried quickly to do So but we cannot declare a pin two times in the .CFG :( I wanted to do it quickly by simply make it follow the principale extruder (there is a new klipper code who allow it now) and activate the servo and release it sometime to remove any tension or synchro. I'm not the best in programmation maybe I should work harder on that!

baccula, 2022-11-15:
Klipper supports duplicate pin configuration (see here
<https://www.klipper3d.org/Config_Reference.html#duplicate_pin_override> for
info). Not sure if that would accomplish what you're looking for or not.

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

RickDnamps, 2022-11-16:
I just try the dupplicate pins like that:

[duplicate_pin_override]
pins: ercf:gpio10, ercf:gpio9, ercf:gpio8, ercf:gpio20

but that doesn't work.

Still have error message:
!pin gpio10 used multiple times in config

Once the underlying issue is corrected, use the "RESTART"
command to reload the config and restart the host software.
Printer is halted!

I try to use the gear stepper motor of the ERCF to help the filament by pushing it and by synchronize it with the main extruder.... if you can help me !!

porklander, 2022-12-28:
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

Do you have success with this?

Anathema-Device, 2022-12-28:
Do you have more than one [duplicate_pin_override] defined maybe?

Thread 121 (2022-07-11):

Use ERCF as bowden extruder?

xeroe, 2022-07-11:
Heyho,
Id like to use the design in my bowden printer.
Do you think it will be possible to use the ercf as the bowden extruder or will i have to reinforce the gear/servo assembly to have more pressure?

Anathema-Device, 2022-07-11:
I don't see why it would not work.  You would need to think of a way to put the filament sensor near the hotend I expect.  Hypothetically the tube lengths may even be shorter requiring less turns on the takeup thus less drag than other arrangements?

EtteGit, 2022-07-17:
It's most likely possible, with some minor software changes. Though, concerning your pressure question, my guess is that this will heavily depends on the speed you want to print at. The higher, the more pressure// grip you'll need.

StanislavJochman, 2023-08-13:
@xeroe Hi. In theory it should be possible, but in practise I would discourage that. There are multipe possible problems.

- Servo would need to be engaged whole time while printing which can lead to it burning out.
- ERCF uses bondech gears for extrusion which is fine for just starting the filament but better solutions exsist for extruders. It would not be hight performance
- Biggest problem which I see is in bouden setup, because multi material printing requires a lot of precesion to be done well and using bouden limits that. It can also cause stringing color bleed and other artefacts.

xeroe, 2023-08-13:
didnt expect an answer after a year but yes i agree with you and ditched the idea :D

StanislavJochman, 2023-08-13:
Please close the issue.

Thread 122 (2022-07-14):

move out of range error after An issue with the ERCF has been detected and the ERCF has been PAUSED. Normal pause resume no issues

rwijnhov, 2022-07-14:
If i normaly pause and resume a print everything works great even in a multi material but if I resume after a:
ERCF is currently paused. Please use ERCF_UNLOCK
Refer to the manual before resuming the print
When you intervene to fix the issue, first call the "ERCF_UNLOCK" Gcode
An issue with the ERCF has been detected and the ERCF has been PAUSED

I always get an move out of range error. This has been driving me mad for days. pls help.

heschlie, 2022-11-08:
@rwijnhov Can you share what you did to resolve this, I'm currently having the exact same issue and am running out of ideas. I assumed it was in relative mode instead of absolute but I tossed in a `G90` in the resume macro and am still seeing this. Thanks!

heschlie, 2022-11-08:
Would you be willing to share your pause/resume macros? I assume that is where my problem is but I am having trouble sorting it out.

Anathema-Device, 2022-11-08:
Make sure that your slicer is using relative extrusion rather than absolute?

rwijnhov, 2022-11-09:
hi i use this on my ratrig 400
############################
####ERCF Cancel Print Resume
#############################
[gcode_macro CANCEL_PRINT]
description: Cancels the printer
rename_existing: CANCEL_PRINT_BASE
gcode:
  END_PRINT
  TURN_OFF_HEATERS
  CLEAR_PAUSE
  #SDCARD_RESET_FILE
  SET_FILAMENT_SENSOR SENSOR=encoder_sensor ENABLE=0
  CANCEL_PRINT_BASE

[gcode_macro PAUSE]
description: Pauses the printer
rename_existing: PAUSE_BASE
variable_extrude: 1.5
gcode:
  SAVE_GCODE_STATE NAME=PAUSE_state
  # Define park positions
  {% set E = printer["gcode_macro PAUSE"].extrude|float %}
  {% set speed = printer["gcode_macro RatOS"].macro_travel_speed|float * 60 %}
  # Calculate safe Z position
  {% set max_z = printer.toolhead.axis_maximum.z|float %}
  {% set act_z = printer.toolhead.position.z|float %}
  {% if act_z < (max_z - 2.0) %}
      {% set z_safe = 2.0 %}
  {% else %}
      {% set z_safe = max_z - act_z %}
  {% endif %}
  PAUSE_BASE
  G91
  # Retract
  {% if printer.extruder.can_extrude|lower == 'true' %}
    G1 E-{E} F2100
  {% else %}
    {action_respond_info("Extruder not hot enough")}
  {% endif %}
  # Move to park position
  G90
  {% if "xyz" in printer.toolhead.homed_axes %}
    G1 Z{z_safe} F900
    _PARK LOCATION={printer["gcode_macro RatOS"].pause_print_park_in} X={printer["gcode_macro RatOS"].pause_print_park_x}
  {% else %}
    {action_respond_info("Printer not homed")}
  {% endif %}

[gcode_macro RESUME]
rename_existing: BASE_RESUME
gcode:
    {% if printer.ercf.is_paused|int == 1 %}
        M118 You can't resume the print without unlocking the ERCF first.
        M118 Run ERCF_UNLOCK and solve any issue before hitting Resume again
    {% else %}
        RESTORE_GCODE_STATE NAME=PAUSE_state
        G90
        {% if printer.ercf.clog_detection|int == 1 %}
            SET_FILAMENT_SENSOR SENSOR=encoder_sensor ENABLE=1
        {% endif %}
        BASE_RESUME
    {% endif %}

heschlie, 2022-11-09:
Thanks @rwijnhov I also decided to try out the sensorless branch (didn't realize that was a thing) and that seems to have fixed it for me. I'm glad to see another ratrig user adding an ERCF to their machine!

Closed 2022-07-14.

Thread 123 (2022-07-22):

More robust _ERCF_CALIBRATE_SINGLE

eamars, 2022-07-22:
Hello
I've been trying to calibrate the ERCF for single tool. I noticed in the _ERCF_CALIBRATE_SINGLE function it assumes the calibration distance and set to 400 fixed.

            M118 Calibrating reference tool {params.TOOL}
            ERCF_LOAD LENGTH={printer["gcode_macro _ERCF_VAR"].min_bowden_length} MOVES={printer["gcode_macro _ERCF_VAR"].num_moves}
            ERCF_HOME_EXTRUDER TOTAL_LENGTH=400 STEP_LENGTH=0.5

This might work in most cases. However with my dual inline extruder, there are about 1500mm distance between the first extruder to the toolhead sensor. I that case I'd propose this function to look at the "end_of_bowden_to_sensor" variable plus some margin to improve the robustness of the calibration routine. For example:

`            ERCF_HOME_EXTRUDER TOTAL_LENGTH={printer["gcode_macro _ERCF_VAR"].end_of_bowden_to_sensor + 400} STEP_LENGTH=0.5
`

eamars, 2022-07-22:
If you think this is a good idea then I can create a PR for this change.

Closed 2022-08-04.

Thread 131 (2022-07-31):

Acceleration when synchronize toolhead and manual stepper

eamars, 2022-07-31:
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
When toolhead and gear stepper is asked to move synchronously, the short move acceleration is specified to the gearstepper while the toolhead keeps its own acceleration. I suspect this could cause "Timer too close" issue when the microstep is setting beyond 16.

In this case my solution is to set the same acceleration that toolhead uses to the gearstepper. This fix allows me to set more than 16 microsteps when initializating the gear stepper.

Do you guys have any comment here?

EtteGit, 2022-08-04:
We could indeed match both motors accels, that looks like the most logical option.

Though the accel difference is not supposed to cause any issues. The "Timer too close" on high microsteping is just the result of the high microsteping itself : it takes longer for the system to generate the steps, and they are sent a tiny bit too late, hence the error.

Same issue arises if you increase the microsteps on the x or y stepper for instance.

eamars, 2022-08-04:
Thanks for the heads up. I tends to agree with your conclusion that the microcontrollers can't keep up. However I do observe the timer too close issue can be minimised when two steppers are sharing the same acceleration.

I'll continue monitoring this issue on my branch of the ERCF driver.

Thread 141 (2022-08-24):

Skipping the Daughter Board?

Durahl, 2022-08-24:
Is it possible - with a Gear Ratio MOD to the ERCF - to run both the ERCFs Gear _**Motor**_ and the Tool Heads Extruder _**Motor**_ in Sync with each other and thus off the same Stepper _**Driver**_?

I'm currently using a **BTT _Octopus V1.1_** on a **_Voron 2.4_** together with an _**ERCF Easy Board**_ but the latter is giving me grief as in the past two weeks or so every once in a while the system is loosing its connection to it which brings me to the idea of using the Octopus for the ERCF as well after all but with it only having 8 Stepper _**Drivers**_ ( _but_ 9 _**Connectors**_ ) and the Voron 2.4 already using 7 of those _**Drivers**_ we're technically 1 short unless we're using the 2 Connectors that share the same Driver for both the ERCF Gear Motor and the Extruder Motor?

Would this be a viable solution? 🤔
My thinking is that the ERCF Servo would disengage from the Filament anyway after the latter was loaded so even if for whatever reason the two BMGs wouldn't be perfectly in sync it shouldn't really matter, right?

If possible, can this be done by only changing the Pins for the Gear Motor to the respective ones on the Octopus or would this also require modifications to the code?

LostFool, 2023-07-04:
I'd love to know if you tried this and got results.

Durahl, 2023-07-05:
[Happy Hare V3](https://github.com/moggieuk/ERCF-Software-V3) - which I've been running on my Setup for a while now ( and which I can **_HIGHLY_** recommend! ) - now seems to be running this very feature in their latest 1.3.0 Release but I have so far not tested it with it being enabled in most parts because the issue from my OP has been resolved by ditching the ERCP for a DIY Solution that does away with a lot of friction causing elements.

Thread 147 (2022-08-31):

no_toolhead_sensor filament load sequence to extruder gear - enhancement

ningpj, 2022-08-31:
I run 250mm/s+ long move speeds and on occasion a slight encoder skip/miss read "seems" to cause the filament spear to ram into the gears at pace.  I currently manually reduce the calibration length for tool 0 by a couple of mm to reduce this risk and subsequent stress on ERCF/toolhead/filament. Slow homing moves to extruder takes care of the rest and are using 1mm rather than 2mm moves to try to reduce some of the tension on the filament path.

I also have aspirations of being able to feed TPU 95 Shore in the future and expect results may be less predictable with a more compressible filament (will test over the weekend).

While I can work around this by manually changing the calibration length, IMHO I think it would be good to change the process to pull up short and creep up at a slower pace rather than risk ramming the extruder and breaking spear tips or the filament itself. You could also potentially consider lowering the gear stepper current for the final creep_to_extruder step then reset it once loaded. There there should be enough filament slack in the bowden tube to enable this without causing subsequent feed issues.

Awesome work BTW.  Really appreciated.

nigelpjames, 2022-09-08:
Dropping the current and restoring it would also allow people to run higher currents or more powerful steppers to drag filament through longer bowden tubes and less free running buffers.

Closed 2024-11-06.

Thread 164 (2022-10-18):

Issue with long_moves_speed

Durahl, 2022-10-18:
I'm kinda having an issue with the in the `ercf_software.cfg` found `long_moves_speed` default setting of `100 mm/s` not working out for me anymore requiring me to lower it down to 60 mm/s as otherwise the Stepper will loose all Steps after managing to pull the Filament for like only 50mm.

The Stepper is an ( I guess ) [OSMTEC 14HS11-1004S](https://www.osmtec.com/14HS11-1004S) powered by a **_BTT TMC2209_** sitting on an [ERCF EASY BRD](https://github.com/Tircown/ERCF-easy-brd) powered via **_MeanWell HDR-60-12_** PSU I had lying around instead of the large 200W 24V one the rest of the System runs on ( the issue was also observed with a **_MOONS MS17HD7L408C-01_** and a spare 2209 Driver ):
```
[manual_stepper gear_stepper]
step_pin: ercf:PA4
dir_pin: ercf:PA10
enable_pin: !ercf:PA2
rotation_distance: 22.2500000
gear_ratio: 80:20
microsteps: 16
full_steps_per_rotation: 200
velocity: 35
accel: 150
endstop_pin: ^ercf:PA7

[tmc2209 manual_stepper gear_stepper]
uart_pin: ercf:PA8
uart_address: 0
interpolate: False  #True
run_current: 0.70
hold_current: 0.40
sense_resistor: 0.110
#stealthchop_threshold: 500
```
The PTFE Tube leading to the Toolhead is a 4mm OD / 3mm ID one with the Spools now using an open section as a no friction "buffer" so there's nothing hardware wise that could cause this:
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

The Gear Stepper Shaft is straight and driven by a machined 80T Gear running absolutely true with no binding and - IMHO - no discernable resistance when the belt is not applied.

Any suggestions what could cause this - Is a component on the EASY Board faulty that allows it to run at low speeds but not high ones? 🤔
```
long_moves_speed: 60 # mm/s. Default value is 100mm/s.
long_moves_accel: 400 # mm/s². Default value is 400mm/s²
short_moves_speed: 30 # mm/s. Default value is 25mm/s.
short_moves_accel: 400 # mm/s². Default value is 400mm/s²
```
On a somewhat related question... ( Because of a different issue ) I'm planning on converting the Toolhead to a CAN Bus System which would free up another Stepper Driver Port on the **_BTT Octopus V1.1_** I'm running my V2.4 opening up the possibility of running the ERCF entirely off the Octopus as well in case of the EASY Board being the culprit ( also making it easier to procure a replacement if the ERCF Fad and replacements for it have run dry 😁 )

The on Page 86 of the Manual described **_SKR 1.3_** appears to have a dedicated Servo PWM Header...
Any information on how this would be handled on a board like the Octopus? [Do we use the J43 ( PB6/PB7 ) normally used for a BLTouch?](https://github.com/bigtreetech/BIGTREETECH-OCTOPUS-V1.0/raw/master/Hardware/BIGTREETECH%20Octopus%20-%20PIN.pdf)
( Not familiar with them but I keep hearing _they_ have Servo inside them soo....? )

128keaton, 2022-11-03:
@Durahl any digital I/O pin should work for the Servo control pin, I used the BL-touch specific headers on my board to control servo/intake from encoder just fine. You can really use _any_ board that runs klipper, I used an SKR Pico to drive mine.

I had a similar issue and went up __2__ top hat locker sizes (3 -> 5) but my filament is getting chewed up slightly.

I would double check your servo angles as well since you really want the stepper to lock into place without it bouncing back from load. If the arm is not fully engaged/parallel to the end of the locker, it will slip.

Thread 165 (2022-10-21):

2x filament tubes to a Y-splice @ the hotend for much faster swaps?  (Asynchronous retraction/extrusion for all but the short distance after the Y to the toolhead)

michael-jennings, 2022-10-21:
Is this an original idea or has this already been discussed (and rejected or planned for the future?):

It looks like running 2 filament tubes to a Y splice at the hotend would significantly increase switching speed.  You could have the next filament queued up near the hotend, and only have to wait for the last filament to retract past the Y splice before extruding the next one in.

While I'm here, my next idea is if we had a mechanism at the ERCF end that would then have another Y configuration that worked like how train tracks can be switched between a left or right split - It would switch the path from the hotend-bound tube, to an open-air cutter that drops a length off in a tray, ensuring a clean tip.  Then it would continue extruding fully, switch the Y back to the normal airtight hotend path, and a rubber membrane could help keep outside air from flowing into the spool upline (for avoiding humidity).

Finally, for purging I am wondering if a brute force mechanism would work for blasting the heatbreak & nozzle clean, avoiding the extra purging required when a new filament is pushing out old filament left inside - For example, if the tube leading into the extruder had a mechanism where it could reliably be pulled out / moved out of the way, so a high-temp tube could do basically the same thing you do when you clean a clogged nozzle with a blow torch (appropriate for the temp tolerance of the nozzle/heatbreak of course), and maybe if that isnt enough, a combination of water mist & high pressure heated air, then cleared of water with a final air-blast.

Heck, you could it move the nozzle over a purge station holding both the entire blast-out and even a blast-in system to do a fast brute force push/pull/incineration process, and the station would then reseat the filament tube into the extruder and there'd be no extra weight on the tool head.

RomRider, 2022-10-21:
> It looks like running 2 filament tubes to a Y splice at the hotend would significantly increase switching speed. You could have the next filament queued up near the hotend, and only have to wait for the last filament to retract past the Y splice before extruding the next one in.

How would that work as there is only 1 cart and the cart can't move while a filament goes through?

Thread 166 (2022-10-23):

Printer pausing after every toolchange without error message

TIMMOOOH, 2022-10-23:
Hello,

when loading the first tool at the beginning of a print, it doesn't pause. But after that it pauses after every Toolchange and parks the toolhead. When resuming manually every time, it works but that is not an option for me.
I looked at the log and right after completing the toolchange it does this "Exiting SD card print (position 2711)" as seen in klippy.1.log. Note: _ ERCF_PAUSE is not triggered, i can resume without problem.

I took the klippy.log right after it paused after a toolchange.
I included all the config files and the macros i took straight from the example macros.

can someone help me please? I'm struggling with that problem since one week.

Files:
[mainsail_console.txt](https://github.com/EtteGit/EnragedRabbitProject/files/9846695/mainsail_console.txt)
[client_macros.txt](https://github.com/EtteGit/EnragedRabbitProject/files/9846696/client_macros.txt)
[ercf_software.txt](https://github.com/EtteGit/EnragedRabbitProject/files/9846697/ercf_software.txt)
[mainsail.txt](https://github.com/EtteGit/EnragedRabbitProject/files/9846698/mainsail.txt)
[printer.txt](https://github.com/EtteGit/EnragedRabbitProject/files/9846699/printer.txt)
[klippy(1).log](https://github.com/EtteGit/EnragedRabbitProject/files/9846693/klippy.1.log)

TIMMOOOH, 2022-10-23:
Just found the cause myself. I feel kinda stupid now.

klippy log showed "Filament Sensor toolhead_sensor: runout event detected, Time 1187.41" while printing.
I just had to removr the "#" in front of "pause_on_runout: False" in the [filament_switch_sensor toolhead_sensor] section in the ercf_hardware.cfg.

I don't know if it's my fault, but i suggest that klipper should do a M118 whet it pauses because of this.

Closed 2022-10-23.

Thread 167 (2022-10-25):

Encoder cart tolerance/clearance issue

SkiBikePrint, 2022-10-25:
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

Design tolerance between bearing and printed part is only 0.2mm per the circled area in the attached picture.  The printed part was too tight and prohibiting the bearing from turning.  Expected print tolerances create likely interference.  The part in the picture has been filed to open up the clearance.

There does not seem to be a design requirement to have the spacing so tight.  I would suggest opening up the clearance to at least 0.5mm or a minimum radius of 5.5mm for the bearing pocket.

Thanks, Glenn
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

jwhite, 2022-11-07:
@SkiBikePrint Can you submit a pull request with your proposed changes?

SkiBikePrint, 2022-11-07:
Hi Jeremy,

I submitted a pull request.  I have never done one before so don't know if I did it right.  Although I created edited STL's I don't know how to attach them so I included them in this email.  Let me know if there is more I need to do.

Thanks,

Glenn
________________________________
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

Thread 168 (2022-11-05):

"a filament sensor system located below the extruder gears" vs Direct Drive Extruder on Printer?

theschles, 2022-11-05:
Hi there, I have a Sovol SV-01 running Klipper, which has a direct-drive extruder -- and no room for a filament sensor between the printer's extruder gears and the hot-end.

When you say "The filament sensor : a filament sensor system located below the extruder gears", to which extruder are you referring?

* The printer's own extruder?
  * ...which would mean that I can't get the ERCF for my printer...
-- or --
* The extruder on the ERCF?
  * ...which would mean my printer would work: Spools -> ERCF -> Filament Sensor -> Direct Drive Extruder -> Hot End

Thanks for the clarification in advance!

RomRider, 2022-11-05:
It's supposed to be after the toolhead extruder, however it's not required anymore if you use the "no_toolhead_sensor" branch

theschles, 2022-11-06:
> It's supposed to be after the toolhead extruder, however it's not required anymore if you use the "no_toolhead_sensor" branch

Apologies, I'm still learning the terminology...when you say "toolhead extruder", you're referring to the 3D printer's extruder, correct?

opiswahn, 2022-11-21:
@theschles The toolhead is usually the thing your hotend is in, if you have DirectDrive then the Extruder is included. The whole assembly is called a tool (hence the name Toolchanger, eg. from E3D)

Closed 2022-11-21.

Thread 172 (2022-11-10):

Tophat servo not working

Outofbox11, 2022-11-10:
Has anyone had issue with servo for tophat not working?  When commanded I hear faint buzz and nothing moves.  checked voltage from EASY BRD V1.1 and it does have 5V.  I have also tried 5 new MG90S servos and same thing.  I went through reflash and reinstall.  everything works except for that servo.  any help would be appreciated.

Outofbox11, 2022-11-10:
figured it out. servo section of the board is bad. reconfigured and connected servo to my spider board and it works fine.

Closed 2022-11-10.

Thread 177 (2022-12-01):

PLA on ERCF?

BoredFishRE, 2022-12-01:
I really can't do ABS, so for anyone that did print in PLA, is there anything I should do for PLA? For the test print, scaling it down by 5% seems to make the heat set insert fit properly, though I don't know if I should do that since I don't know if it'll make any clearance issues.

RomRider, 2022-12-01:
I printed in PETG, no difference and no modifications. 5% is A LOT. Either you don't have the right inserts or your printer is not calibrated.
Use a caliper instead and compare against the CAD.

BoredFishRE, 2022-12-01:
> I printed in PETG, no difference and no modifications. 5% is A LOT. Either you don't have the right inserts or your printer is not calibrated. Use a caliper instead and compare against the CAD.

ah. I just checked cad, it's 4.7mm and the CNC kitchen heat set inserts i'm using are 4.6mm in dia, so that may be my problem

RomRider, 2022-12-01:
Heat inserts are M3xD5xL4, you can find them on AliExpress

BoredFishRE, 2022-12-01:
I got a kit from dfh, so I think I'll be Good

Closed 2022-12-01.

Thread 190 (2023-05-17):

Is it possible to use ERCF without toolhead sensor?

Caos-Maker89, 2023-05-17:
Hi,
I have a sidewinder x1 with klipper.
Is it possible to use ERCF without the toolhead sensor?

Thank you

nigelpjames, 2023-05-17:
Yes, most of us already use sensorless filament homing when loading which progressively advances the filament until it hits extruder gears and stops when the encoder doesnt detect further movement before commencing the hotend load sequence
].  Theres also an  option to drop run_current while homing on the ERCF gear stepper to lessen the impact and risk of grinding filament.

Caos-Maker89, 2023-05-17:
thank u very much @nigelpjames !

Closed 2023-05-17.

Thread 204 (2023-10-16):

tolerances of .stl parts good for resin printing?

o-lampe, 2023-10-16:
Often, parts designed for FDM printers come with a *fudge factor* for more precise inner diameters and bridging.
If I print ERCF parts with a resin printer, will they fit together or are too loose or tight?
THX
O-Lampe

ammoniak, 2023-10-26:
There is a calibration part, The documentation/manual explains the features and what you need to messure/test. If the clibration part works, the rest should too.

o-lampe, 2023-11-08:
The calibration part worked fine, but there are so many M3 heat-set inserts, which won't work with resin-printed parts.

Kadah, 2023-12-27:
> The calibration part worked fine, but there are so many M3 heat-set inserts, which won't work with resin-printed parts.

You could try over-sizing those holes and setting the inserts with resin.

I had a quick google and CNC Kitchen did a vid on this very topic last year.
https://www.youtube.com/watch?v=4nbvU2kGzxc

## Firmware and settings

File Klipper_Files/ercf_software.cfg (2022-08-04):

###############################
# ERCF module
###############################

[ercf]
# Encoder 
encoder_pin: ^P1.0
encoder_resolution: 1.365188 # in mm
# Speeds and accels
# Long moves are faster than the small ones
# 100mm/s should be "quiet" with the NEMA14 motor or a NEMA17 pancake, but you can go lower if your really want it to be low noise
# Tested without any issue at 200mm/s, but it's noisy. I'm running mine at 170mm/s for long moves and 50mm/s for short moves.
long_moves_speed: 100 # mm/s. Default value is 100mm/s.
long_moves_accel: 400 # mm/s². Default value is 400mm/s²
short_moves_speed: 25 # mm/s. Default value is 25mm/s.
short_moves_accel: 400 # mm/s². Default value is 400mm/s²

[gcode_macro _ERCF_VAR]
description: Empty macro to store ERCF variables
# =======================================================
# ================== VALUES TO ADJUST ===================
# =======================================================
#
# ==== Toolhead specific values ====
#
# Distance between the end of the reverse bowden and the toolhead sensor. Value is toolhead specific.
# Tested values :
# Galileo Clockwork with ERCF V1.1 sensor (hall effect) : 27.0
# LGX on AfterBurner with ERCF V1.1 sensor (hall effect) : 44.0
# AfterBurner Clockwork with ERCF V1.1 sensor (hall effect) : 36.0
variable_end_of_bowden_to_sensor: 27.0
# Length from the sensor to the nozzle melt pool.
# Reduce this value if there are blobs of filament on each load, before the purge on the tower.
# Increase this value if there are big gaps on the purge tower (i.e. if it takes time for the filament to get pushed out after a swap)
# Tested values :
# Galileo Clockwork with ERCF 1.1 sensor (hall effect) & Dragon Normal Flow : 60.5
# LGX on AfterBurner with ERCF 1.1 sensor (hall effect) & Dragon Normal Flow : 55.6
# AfterBurner Clockwork with ERCF 1.1 sensor (hall effect) & Dragon Normal Flow : 54.0
variable_sensor_to_nozzle: 60.5  
#
# ==== Values to tune ====         
#
# Tool position for the selector. This has to be tuned manually. Please scale this array to the number of tools you have
variable_colorselector = [2.4, 24.0, 44.8, 71.2, 92.0, 113.6, 139.2, 160.8, 181.6]
# Base value for the loading length used by the auto-calibration macro
# Please use a value SMALLER than the real reverse bowden length (like 50mm less)
variable_min_bowden_length: 750.0
# Servo angle for the Up position (i.e. tool disengaged). Refer to the manual to know how to properly tune this value
# Default values:
# MG90S servo : 30
# SAVOX SH0255MG : 140
variable_servo_up_angle: 30
# Servo angle for the Down position (i.e. tool engaged). Refer to the manual to know how to properly tune this value
# Default values:
# MG90S servo : 140
# SAVOX SH0255MG : 30
variable_servo_down_angle: 140
# Threshold for the final load check (i.e. the move from the toolhead sensor to the nozzle)
# Check the _ERCF_GET_LOAD_THRESHOLD command to get the proper value for your setup
variable_final_load_check_threshold: 10.0
# Options to use or not 
# Beware that the clog detection and endless spool mode are in BETA mode for now
# Use at your own risk (beware of the involved macros and the pause(s) and resume ones)
# Put 0 to disable, 1 to enable
variable_clog_detection: 0
variable_endless_spool_mode: 0
variable_sensorless_selector: 0
# The hair puller move is an extruder move that extrudes during an unload,
# right before the long unload move done by the ercf. The purpose is to pull off any 
# potential long hair from the filament tip. This small extrusion move is done after
# the ercf has already unloaded the length defined by the unload_move_before_hair_pulling.
# Put 0 to disable, 1 to enable
variable_hair_puller_move: 0
variable_unload_move_before_hair_pulling: 20.0

# =======================================================
# ============ END OF VALUES TO ADJUST ==================
# =======================================================
# You shouldn't have to change anything below this point

# Things that you shouldn't have to change
variable_unload_modifier: 9.0                                                               # Modifier to adjust the ERCF park position (where the filament ends when doing an unload)
variable_min_temp_extruder: 180                                                             # Temp used during the auto-calibration macro, to ensure we can move the extruder (but not really extruding)
variable_extruder_eject_temp: 240                                                           # Temp used during filament ejection (in the ERCF_HOME macro, if a filament is detected in the toolhead)
variable_timeout_pause: 72000                                                               # Time out used by the _ERCF_PAUSE
variable_disable_heater: 600                                                                # Delay after which the hotend heater is disabled in the _ERCF_PAUSE state
variable_gear_stepper_accel: 0                                                              # The acceleration value applied to the gear stepper on moves, standard is to use 0
variable_extra_servo_dwell_up: 0                                                            # Additional dwell time in ms to apply to dwell prior to turning off the servo
variable_extra_servo_dwell_down: 0                                                          # Additional dwell time in ms to apply to dwell prior to turning off the servo
variable_num_moves: 1                                                                       # Nunber of moves to use for load/unload. Increase to 2 or 3 to prevent 'Timer too close' error
gcode:

[save_variables]
filename: /home/pi/klipper_config/ercf_vars.cfg

###############################
# ERCF Calibration macros
###############################
[gcode_macro _ERCF_CALIB_SELECTOR]
description: Calibration of the selector position for a defined Tool
gcode:
    _ERCF_SERVO_UP

    {% set move_length=(20.0 + (params.TOOL|int + 1)*21.0 + ((params.TOOL|int + 1)/3)*5.0) %}

    M118 Measuring the selector position for tool {params.TOOL}
    ERCF_GET_SELECTOR_POS REF={move_length|int}
    
    _ERCF_MOTORS_OFF

[gcode_macro _ERCF_CALIBRATE]
description: Complete calibration of all ERCF Tools
gcode:
    SET_FILAMENT_SENSOR SENSOR=encoder_sensor ENABLE=0
    M118 Start the complete auto calibration...
    M118 First home the ERCF
    ERCF_HOME

    {% for chan in range(printer["gcode_macro _ERCF_VAR"].colorselector|length) %}
            _ERCF_CALIBRATE_SINGLE TOOL={chan|int}
    {% endfor %}

    M118 End of the complete auto calibration!
    M118 Please reload the firmware for the calibration to be active!

[gcode_macro _ERCF_CALIBRATE_SINGLE]
description: Calibration of a single ERCF Tool
gcode:
    SET_FILAMENT_SENSOR SENSOR=encoder_sensor ENABLE=0
    {% if params.TOOL|int >= 0 and params.TOOL|int < printer["gcode_macro _ERCF_VAR"].colorselector|length %}
        {% if printer["gcode_macro ERCF_HOME"].home == -1 %}
            M118 First home the ERCF
            ERCF_HOME
        {% endif %}

        _ERCF_SELECT_TOOL TOOL={params.TOOL}
        ERCF_SET_STEPS RATIO=1.0

        {% if params.TOOL|int == 0 %}
            {% if printer['extruder'].temperature < printer["gcode_macro _ERCF_VAR"].min_temp_extruder %}
            M109 S{printer["gcode_macro _ERCF_VAR"].min_temp_extruder|int}
            {% endif %}

            M118 Calibrating reference tool {params.TOOL}
            ERCF_LOAD LENGTH={printer["gcode_macro _ERCF_VAR"].min_bowden_length} MOVES={printer["gcode_macro _ERCF_VAR"].num_moves}
            ERCF_HOME_EXTRUDER TOTAL_LENGTH={printer["gcode_macro _ERCF_VAR"].end_of_bowden_to_sensor|float + 400} STEP_LENGTH=0.5
            
            _ERCF_CALIB_SAVE_VAR TOOL={params.TOOL}

            G91
            G92 E0
            MANUAL_STEPPER STEPPER=gear_stepper SET_POSITION=0
            MANUAL_STEPPER STEPPER=gear_stepper MOVE=-{printer["gcode_macro _ERCF_VAR"].end_of_bowden_to_sensor|float} SPEED=25 ACCEL={printer["gcode_macro _ERCF_VAR"].gear_stepper_accel|int} SYNC=0
            G1 E-{printer["gcode_macro _ERCF_VAR"].end_of_bowden_to_sensor|float} F1500.0

            _ERCF_CALIB_UNLOAD
            ERCF_BUZZ_GEAR_MOTOR
            _ERCF_IS_FILAMENT_STUCK_IN_ERCF
            
            _ERCF_UNSELECT_TOOL
        {% else %}
            M118 Calibrating tool {params.TOOL}

            ERCF_LOAD LENGTH={printer["gcode_macro _ERCF_VAR"].min_bowden_length|float - 100.0} MOVES={printer["gcode_macro _ERCF_VAR"].num_moves}
            _ERCF_CALIB_SAVE_VAR tool={params.TOOL}

            _ERCF_CALIB_UNLOAD LENGTH={printer["gcode_macro _ERCF_VAR"].min_bowden_length|float - 100.0 + 27.0} MOVES={printer["gcode_macro _ERCF_VAR"].num_moves}
        {% endif %}

    {% else %}
        M118 Tool out of range
    {% endif %}
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

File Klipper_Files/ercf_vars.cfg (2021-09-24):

[Variables]
ercf_calib_0 = 1.0
ercf_calib_1 = 1.0
ercf_calib_2 = 1.0
ercf_calib_3 = 1.0
ercf_calib_4 = 1.0
ercf_calib_5 = 1.0
ercf_calib_6 = 1.0
ercf_calib_7 = 1.0
ercf_calib_8 = 1.0
ercf_calib_9 = 1.0
ercf_calib_10 = 1.0
ercf_calib_11 = 1.0
ercf_calib_ref = 500.0

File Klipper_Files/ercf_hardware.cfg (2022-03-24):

## Enraged Rabbit : Carrot Feeder V1.1 hardware config file
# Values are an example for voron 2.4 with 2 SKR1.4

# Carrot Feeder 5mm D-cut shaft
# Example for an SKR 1.4 Board (E1 on the XY mcu)
[manual_stepper gear_stepper]
step_pin: P1.15
dir_pin: P1.14
enable_pin: !P1.16
rotation_distance: 22.6789511	#Bondtech 5mm Drive Gears
gear_ratio: 80:20
microsteps: 16  # Please do not go higher than 16, this can cause 'MCU Timer too close' issues under Klipper
full_steps_per_rotation: 200	#200 for 1.8 degree, 400 for 0.9 degree
velocity: 35
accel: 150
#Right now no pin is used for the endstop, but we need to define one for klipper. So just use a random, not used pin
endstop_pin: P0.10

[tmc2209 manual_stepper gear_stepper]
# Adapt accordingly to your setup and desires
# The default values are tested with the BOM NEMA14 motor
# Please adapt those values to the motor you are using
# Example : for NEMA17 motors, you'll usually set the stealthchop_threshold to 0
# and use higher current
uart_pin: P1.1
interpolate: True
run_current: 0.40
hold_current: 0.1
sense_resistor: 0.110
stealthchop_threshold: 500 

[tmc2209 manual_stepper selector_stepper]
uart_pin: P1.8
run_current: 0.55
interpolate: True
sense_resistor: 0.110
stealthchop_threshold: 500
# Uncomment the lines below if you want to use sensorless homing for the selector
#diag_pin: ^P1.27      # Set to MCU pin connected to TMC DIAG pin
#driver_SGTHRS: 75  # 255 is most sensitive value, 0 is least sensitive

# Carrot Feeder selector
# Example for an SKR 1.4 Board (Z1 on the XY mcu)
[manual_stepper selector_stepper]
step_pin: P0.22
dir_pin: P2.11
enable_pin: !P0.21
microsteps: 16    # Please do not go higher than 16, this can cause 'MCU Timer too close' issues under Klipper
rotation_distance: 40
full_steps_per_rotation: 200	#200 for 1.8 degree, 400 for 0.9 degree
velocity: 200
accel: 600
# Select the endstop you want depending if you are using sensorless homing for the selector or not
endstop_pin: P1.25
#endstop_pin: tmc2209_selector_stepper:virtual_endstop

# Values are for the MG90S servo
[servo ercf_servo]
pin: P1.26
maximum_servo_angle: 180
minimum_pulse_width: 0.00085
maximum_pulse_width: 0.00215

[duplicate_pin_override]
pins: P1.0
# Put there the pin used by the encoder and the filament_motion_sensor
# It has to be the same pin for those 3

[filament_motion_sensor encoder_sensor]
switch_pin: ^P1.0
pause_on_runout: False
detection_length: 10.0
extruder: extruder
# runout_gcode: _ERCF_ENCODER_MOTION_ISSUE

[filament_switch_sensor toolhead_sensor]
pause_on_runout: False
switch_pin: ^P1.27 

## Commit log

2021-02-03 Add files via upload
    - Added Filament Detector for Galileo Toolhead STLs
    [Filament_Sensor_Lever.stl, Galileo_Body_ECAS_Filament_Sensor.stl, Galileo_Body_M10_Filament_Sensor.stl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]
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2021-02-06 - STLs for Carrot Warehouse V1.0 - Assembly manual for the Carrot Warehouse
    [608_Adapter.stl, Buffer_Axis.stl, Buffer_Cross.stl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]
2021-02-06 - Fixed the missing built-in support in the Main_Body.stl
    [Main_Body.stl]
2021-02-07 - Fixed the overhang issue on the spool arm
    [Spool_Arm.stl]
2021-02-07 - Added a long version of the spool arm to fit big spools. This part has not been tested yet.
    [Spool_Arm_Long.stl]
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2021-02-17 - Added the step file for the filament detector for the Galileo Clockwork
    [Filament_Detector_Galileo.step]
2021-02-18 - Added the Back panel connector for the Voron V2 (to plug the ERCF into)
    [V2_Plug_Panel_ERCF.stl]
2021-02-18 - Fixed orientation issue on the ERCF back panel
    [V2_Plug_Panel_ERCF.stl]
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2021-02-22 - The Carrot Warehouse has been renamed the Carrot Patch - The Carrot Path has been patched, the issue when sometimes the filament would escape from the buffer cage is now fixed
    [608_Adapter.stl, Buffer_Axis.stl, Buffer_Cross.stl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]
2021-02-23 - Fixed the missing built-in support in the Carrot Patch Main Body stl
    [Main_Body.stl]
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2021-03-05 - Updated the filament detector to match the latest Galileo Clockwork version
    [Galileo_Body_ECAS_Filament_Sensor.stl, Galileo_Body_Filament_Detector_ECAS.stl, Galileo_Body_Filament_Detector_M10.stl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]
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2021-03-06 - Added STEP for the Carrot Patch - Updated STEP for the filament detector (Galileo Clockwork)
    [Filament_Detector_Galileo.step]
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2021-03-19 Add new file for Galileo 1.5
    The engine side bearing has a diameter of 16 mm compared to 14 mm for the previous version.
    [Galileo_Clockwork_Latest_ERCF_ECAS_1.5.STL]
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2021-04-05 Rename ir_sensor to toolhead_sensor
    This renames the filament sensor in the toolhead from ir_sensor to
    toolhead_sensor, since it may not be a IR sensor at all.
    [ercf_hardware.cfg, ercf_macros.cfg]
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2021-04-05 Fix formatting of colorselector variable
    This is just to make it consistent with the other variables in this
    section.
    [ercf_macros.cfg]
2021-04-05 Rename `infos` to `ERCF_INFO`
    This renames the `infos` macro to something a bit more informative and
    less likely to conflict with a users existing macros.
    [ercf_macros.cfg]
2021-04-05 Tell people what command to run to unlock
    This changes the homing failed command to tell people the unlock command
    to run, instead of just telling them to unlock.
    [ercf_macros.cfg]
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2021-04-10 Simple typo fix.
    [ercf_macros.cfg]
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2021-04-11 Add unlock instruction to all pause checks
    When the ERCF is locked, it's easy (if you're new at least) to forget to
    unlock it. When this happens and you're trying to fix an issue, all the
    commands silently return with no response. This changes all of the
    pause checks to print out a message about running unlock. This might
    lead to the unlock message being printed more than once in some cases,
    but that's probably better than not at all.
    [ercf_macros.cfg]
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2021-05-13 missing files
    [LGX to AB with ECRF sensor.stl]
2021-05-24 - Replaced spaces by underscores on some usermod folders
    [CartShell.stl, LGX Front Mount v3.stl, LGX Mount ERCF v2.step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]
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2021-06-02 - Released Carrot Patch V1.1. See the repo main page changelog for the details
    [608_Adapter.stl, Buffer_Cross.stl, Main_Body.stl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]
2021-06-04 - Updated the TopHatLockers, TopGearHat and ServoArm to the earlydevaccess branch (much better behavior than the previous version) - Small update on the assembly manual
    [Servo_Arm.stl, Top_Hat_Locker_0.stl, Top_Hat_Locker_m1.stl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]
2021-06-04 - Updated the ercf macros to the earlydevaccess branch version. You may need to retune some ercf variables
    [ercf_macros.cfg]
2021-06-04 - Added missing parts on the new macros
    [ercf_hardware.cfg, printer.cfg]
2021-06-08 Rework folder structure
    [AboveAndBelowGears.step, AboveAndBelowGears_ClockworkBody.stl, AboveAndBelowGears_InternalCover.stl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]
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2021-07-06 - Updated the ercf_macros.cfg for simpler user experience, notably for tuning the load length
    [ercf_macros.cfg]
2021-07-06 Mod: Bearing block passthrough
    This mod allows one to add a passthrough chanel to an ERCF.
    i.e. to use the encoder/runout sensor for single-material prints without changing the spool configuration. Or to daisy chaining multiples ERCF.
    This bearing block is 1mm wider than the original one.
    [Bearing_Block_Passthrough.step, [a]_Bearing_Block_Passthrough.stl.stl]
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2021-07-08 - Fixed a typo in a klipper command
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2021-08-05 - Snapshoted extruder temperature during an ERCF pause is now the target, rather than the current temperature
    [ercf_macros.cfg]
2021-08-12 FIX: fix concatenating string for ERCF_CALIBRATION_DISPLAY
    [ercf_macros.cfg]
2021-08-17 Upload correct STL
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2021-09-17 - Dedicated folder for the ERCP handles - Moved the ERCP manual in the Documentation folder
    [[a]_Handle_0.stl, [a]_Handle_1.stl, [a]_Handle_2.stl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]
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2021-09-21 - Fixed a minor issue on the [a]_Servo_Arm.stl
    [[a]_Servo_Arm.stl]
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2021-09-24 - Added tag plates and magnetic gates with numbering for tools 9 to 11
    [[a]_Magnetic_Gate_10.stl, [a]_Magnetic_Gate_11.stl, [a]_Magnetic_Gate_9.stl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]
2021-09-24 - Added a small calibration test print to help having the printer and slicer properly tuned for the Enraged Rabbit Project parts
    [Calib_Test.stl]
2021-09-24 - New Motor Arm (for NEMA 17 and 14) for the EASY BRD users. Design by Tircown =)
    [Motor_Arm_NEMA14_EASYBRD.stl, Motor_Arm_NEMA17_EASYBRD.stl]
2021-09-24 - ERCF V1.1 macros and python module - Clog detection and endless spool modes are available, but in BETA mode. Use at your own risks
    [client_macros.cfg, ercf_hardware.cfg, ercf_macros.cfg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]
2021-09-24 - New version of the ERCF manual : - Some updates / fixes - Clearer wiring steps for EASY BRD users - Full EASY BRD guide (thanks to Tircown) - Full Setup and Calibration steps
2021-09-24 - Fixed a missing ref to the EASY BRD wiring section
2021-09-24 - Commented the macros related to my own purge bucket // brush on the endless spool mode. Please adapt the macros to your own setup
    [ercf_software.cfg]
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2021-09-30 - Fixed the thread orientation
    [SwitchWire_Mount.stl]
2021-09-30 - Make it mandatory to ERCF_UNLOCK before a Resume in the event of an ERCF_PAUSE
    [client_macros.cfg]
2021-09-30 - Removed the Z move (+ - 3mm) during a filament swap
    [ercf_software.cfg]
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2021-10-05 - Fixed a minor bug in the homing sequence
    [ercf.py]
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2021-10-15 - Added the AfterBurner Clockwork toolhead with the new ERCF hall effect sensor
    [AB_ERCF_Sensor_Extruder_Body.stl, [a]_AB_ERCF_Sensor_Cable_Cover.stl, [a]_AB_ERCF_Sensor_Latch.stl]
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2021-10-23 - Refactor of the ercf.py module - Added descriptions to the ERCF macros - Improved UNLOAD sequence - Misc. improvements
    [client_macros.cfg, ercf_hardware.cfg, ercf_software.cfg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]
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2021-10-28 - Fixed the microsteps in the cfg
    [ercf_hardware.cfg]
2021-10-31 Delete Main_Body_Drybox.stl
    replaced with Main_Body_Drybox V1.1.stl
    [Main_Body_Drybox.stl]
2021-10-31 Add files via upload
    screw in the backside feet has to go the other way around to match the V1.1 Carrot_Patch
    [Main_Body_Drybox V1.1.stl]
2021-10-31 modified for V1.1 Carrot_Patch
    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
    [Main_Body_Drybox V1.1.stl]
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2021-11-05 Carrot patch that can handle a 2.5kg ESUN spool
    Adjustments to Main_Body, Spool_Slider and Cross_Arm to fit an 2.5kg ESUN spool
    [CrossArm_ESUN_2.5kg.stl, Main_Body_ESUN_2.5kg.stl, SpoolSlider_extraLong.stl]
2021-11-10 - Increase the idler height room on the idler to fit Runice idlers
    [Idler_Block.stl]
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2021-11-12 - Increased the room during unload to avoid filament getting stuck in the extruder gears
    [ercf_software.cfg]
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2021-11-19 - Reduced max height of the top hat lockers to avoid hitting the servo body - Added optionnal, high values (6 to 10) Top Hat Lockers
    [Top_Hat_Locker_10_xN.stl, Top_Hat_Locker_5_xN.stl, Top_Hat_Locker_6_xN.stl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]
2021-11-20 - Fixed issues when ercf_software.cfg was included before ercf_hardware.cfg
    [ercf.py]
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2021-11-30 - Fixed an issue where on rare occasions no unload are performed when a tool changed is requested - Added a check for the final load phase (from toolhead sensor to nozzle), making sure the filament w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
    [ercf_software.cfg]
2021-11-30 fix ERCF_LOAD_FILAMENT_IN_EXTRUDER macro
    [ercf_software.cfg]
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2022-01-03 - Fixed minor mesh issue on the knob
    [[a]_Knob.stl]
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2022-01-19 Update ERCF_Software to preserve pressure advance during endless spool mode
    Spool changes drop the pressure advance values to 0, This causes the pressure advance during endless spool mode to go to 0 but it does not ever reset due this being an unplanned change and thus no PA value is issued in gcode again. This saves the PA value before change and applies it again after the change.
    [ercf_software.cfg]
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2022-02-11 fix: use set/get_rotation distance for newer klipper versions since set_step_dist was removed
    [ercf.py]
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2022-02-24 - Fixed minor orientation issues
    [AB_ERCF_Sensor_Extruder_Body.stl, LGX_on_AfterBurner_Adapter_ERCF_Sensor.stl]
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2022-03-16 ERCF_HOME_ONLY Fix message to show actual tool
    [ercf_software.cfg]
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2022-03-21 - Fix for some MCU Timer too close issues with latest Klipper versions
    [ercf.py]
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2022-03-22 - Preparing ercf_hardware.cfg to use stallguard capabilities for the selector cart
    [ercf_hardware.cfg]
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2022-03-22 - New macro naming convention (many macros will be hidden in mainsail//fluidd) - New, simpler and faster, unload sequence during print - Possibility to use 2209 Stallguard for selector cart moves
    [ercf_software.cfg]
2022-03-22 Revert "- Fix for some MCU Timer too close issues with latest Klipper versions"
    This reverts commit 759c0901311cb8517cc6db50071ac5a085ef02ae.
    [ercf.py]
2022-03-23 Update ercf.py
    - Fixed indentation
    [ercf.py]
2022-03-24 - Missing underscores
    [client_macros.cfg]
2022-03-24 - Missing underscore
    [ercf_hardware.cfg]
2022-03-31 Moved homebrew toolhead adapters to usermods per Ette's request. Made 'Too much slippage...' messages more expressive in ERCF.py.
    [ERCF_AB_Orbiter(1v5_&_2)_Adaptor_Back.stl, ERCF_AB_Orbiter1v5_Adaptor_Front.stl, ERCF_AB_Orbiter2_Adaptor_Front.stl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]
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2022-04-04 - Added explicit swap message after a TX call
    [ercf_software.cfg]
2022-04-04 - Fixed unload issue on swaps out of a print
    [ercf_software.cfg]
2022-04-04 - Cleaning the stallguard selector move function
    [ercf.py]
2022-04-05 - Fixed an issue where previous tool wouldn't be reloaded after an ERCF_HOME
    [ercf_software.cfg]
2022-04-07 - Fixed timing issue with toolhead sensor on unloads
    [ercf_software.cfg]
2022-04-07 - Fixed several unload issues
    [ercf_software.cfg]
2022-04-07 - Added fix for some MCU Timer Too close issues on filament load retries
    [ercf.py]
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2022-05-02 Revert "Probably a better change"
    This reverts commit 7f5110c6c0ce6f839d44475560d2dfb0f96af5c0.
    [ercf_software.cfg]
2022-05-03 Don't grind filament if stuck
    [ercf_software.cfg]
2022-05-04 Fix sporadic filament stuck error
    [ercf_software.cfg]
2022-05-04 Better approach to preventing unload
    [ercf_software.cfg]
2022-05-05 adds anchor
    The anchor acts as a further mechanism to hold back the filament.
    Also fixes a geometry error in the STL.
    [[a]_Buffer_Wheel_EZ_Loader.stl]
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2022-05-07 Fix ERCF_LOAD_FILAMENT_IN_EXTRUDER
    [ercf_software.cfg]
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2022-06-17 adding slip rod cover for tubing
    [RepRackErctMount_SlipRod.stl]
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2022-07-24 Fix the eject length calculation
    [ercf_software.cfg]
2022-07-24 Fix the maximum length of the extrusion during calibration
    [ercf_software.cfg]
2022-07-25 Modified the internal washer slot from a horizontal surface to an inclined one.
    The horizontal surface would catch the washer and prevent it from
    egressing into the filament chamber. This change allows the washer
    to easily slide from the holding chamber to the filament chamber.
    [LGX_on_AfterBurner_ERCF_Sensor.step]
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
